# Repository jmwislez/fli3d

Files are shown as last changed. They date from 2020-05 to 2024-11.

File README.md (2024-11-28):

# The Fli3d Project

## Purpose

Fli3d (pronounced "flight") is a project by Jean-Marc Wislez for the 2020 (well, 2022) edition of the Belgian "Fri3d Camp" hacker event (https://www.fri3d.be/). Its purpose is to develop and launch an ESP32 payload on top of a microrocket.  And this payload needs to be as cool as possible ...

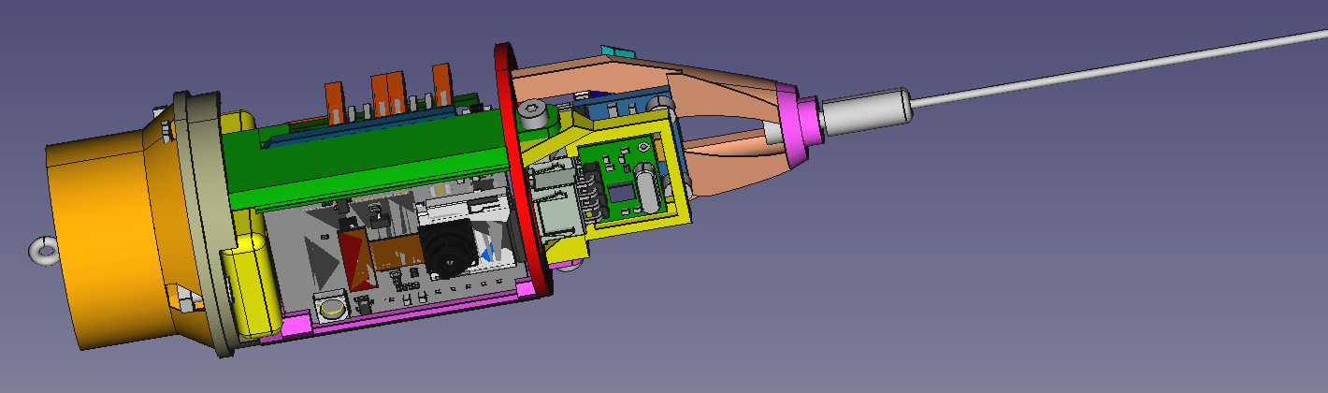
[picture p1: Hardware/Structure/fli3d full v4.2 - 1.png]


The name is obviously derived from "Fri3d Camp", and from the fact it's "flight hardware".

I have been working in the space industry for more than 20 years now, and this included design, building, testing and operations of payloads on Shuttle missions and ISS.  Basically I used this experience and the typical approaches here, but doing everything myself instead of collaborating in large teams.

## Overview

The Fli3d payload has roughly the size of a toilet paper roll, and weighs less than 100g.  Hardware costs for one v1 unit are below 25 euros.  The payload is intended for launch on a microrocket with minimally a B-motor.  The payload contains the following:
  - a 3D-printed structure and fairing
  - an ESP32 minikit MH-ET microprocessor board, running custom software (developed in Arduino IDE) to control all Fli3d subsystems and transmit live telemetry and receive commands over WiFi
  - an MPU6050 accelerometer/gyroscope sensor unit for determining accelerations and orientation
  - a BMP280 barometric sensor for determination of the rocket altitude
  - a NEO6MV2 GPS module, for determination of position and speed
  - an ESP32CAM module with an OV2640 camera and SD-card module, for image acquisition, in-flight image and telemetry storage, and live transmission of telemetry and images over WiFi
  - a WL102-341 433 MHz radio transmitter module, for in-flight transmission of selected telemetry
  - a 240 mAh Li-ION battery for standalone autonomy of 20 (TBC) minutes, with 134N3P charger for tethered operation or pre-launch charging
  - separation detection, for detection of opening of parachute compartment
  
All flight data is to be monitored live on a ground computer running Yamcs (open source software developed for ISS payload and satellite operations), and to be retrievable after flight, both physically and through file transfer.

A v2 version is under development with significantly improved functionality and also easier to assemble and test.  More information will be available soon ...

## Flights

To date, the payload has not flown yet.  It is hoped to do one or more test flights before Fri3d Camp in August 2020, and one or more demo flights at Fri3d Camp.

Each flight will be designated through a successive starting letter, and have a corresponding name:
  - Fli3d Aubergine [flew 18-Aug-2024 on a C-motor microrocket](https://github.com/jmwislez/fli3d/blob/master/Fli3d%20Aubergine%20-%20flight%20report.md)
  - Fli3d Banana 
  - Fli3d Chicken ([flew 25-Sep-2022 on a weather balloon](https://github.com/jmwislez/fli3d/blob/master/Fli3d%20Chicken%20-%20flight%20report.md))
  - Fli3d Dumplings
  - Fli3d Eggs
  - Fli3d Fries
  - ...
  - Fli3d Rice

Fli3d Chicken is not on a micro-rocket, but on a weather balloon.  [A special casing](https://github.com/jmwislez/fli3d/blob/master/HARDWARE.md#structure-for-weather-balloon-version) was developed for this configuration.

## Available documentation and repositories

  - https://github.com/jmwislez/fli3d :
    - Project introduction
    - Hardware design files
    - Yamcs (ground segment software) configuration
  - https://github.com/jmwislez/fli3d_esp32 :
    - Arduino IDE code for fli3d ESP32 MH-ET LIVE MiniKit
  - https://github.com/jmwislez/fli3d_esp32cam :
    - Arduino IDE code for fli3d ESP32-CAM
  - https://github.com/jmwislez/fli3d_lib :
    - Common Arduino IDE code for fli3d ESP32 MH-ET LIVE MiniKit and ESP32-CAM

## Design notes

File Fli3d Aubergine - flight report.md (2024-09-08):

# Fli3d Aubergine – flight report
## Main flight characteristics
Fli3d Aubergine was the first flight of the Fli3d payload on a microrocket.  It was the second flight of the Fli3d electronics. [Click here](https://github.com/jmwislez/fli3d/blob/master/README.md#flights) for an overview of the flights and their naming.

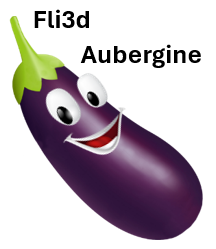
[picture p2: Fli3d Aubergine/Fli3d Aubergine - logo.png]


| Characteristic | Value |
| - | - |
| Launch date / time | 18-Aug-2024 12:41 CEST |
| Launch location | De Kluis, Sint-Joris-Weert, Belgium |
| Height (without antenna) | 50 cm |
| Height (with antenna) | 65 cm |
| Diameter | 35 mm |
| Mass | 145 g |
| Motor | C6-3 |
| Parachute | 45 cm by Klima |
| Fin: | 3D printed (3) |
| Stability number | 4.94 calibre |

[[Fli3d Aubergine photo album](https://photos.app.goo.gl/HriTFwFs2qNNNqe7A)]

## Ground segment
The ground segment set-up consisted of a Windows 10 laptop running [Yamcs 5.9.8](https://yamcs.org), a NodeMCU ESP8266 microcontroller running [fli3d-rx433](https://github.com/jmwislez/fli3d_rx433) for translating the telemetry packets received over radio (433.700 MHz) to UDP packets towards Yamcs, and a WRT-54GL router for creating a private 2.4 GHz Wi-Fi network with fixed IP address assignments for the rocket, laptop and radio receiver.

## System status before launch
The original Fli3d Payload [as described here](https://github.com/jmwislez/fli3d/blob/master/HARDWARE.md#fli3d-hardware) was flown.

The rocket software was way more stable than during Fri3d Camp 2022.  This is mainly thanks to some bug fixing, code clean-up to eliminate all compilation warnings for the Fli3d native code, and porting to the latest ESP32 core (v3.0.4) and libraries.  The software version was as below (tagged "aubergine" in repositories):

| Subsystem | Software version |
| - | - |
| ESP32 | [fli3d_esp32](https://github.com/jmwislez/fli3d_esp32/) v1.2.0 dated 2-Aug-2024 <br /> [fli3d_lib](https://github.com/jmwislez/fli3d_lib/) v1.2.2 dated 13-Aug-2024 |
| ESP32CAM | [fli3d_esp32cam](https://github.com/jmwislez/fli3d_esp32cam/) v2.2.0 dated 2-Aug-2024 <br /> [fli3d_lib](https://github.com/jmwislez/fli3d_lib/) v1.2.2 dated 13-Aug-2024 |

The only subsystem not working was the NEO6mv2 GPS receiver, that would not lock for unknown reasons.  This is an intermittent problem which I did not yet try to debug.  It is possibly linked to the positioning of the GPS antenna too close to other electronics (though it used to mostly work in the past).

The final assembly of the payload and rocket were achieved only just before flight. I had no time to do any further testing or preparations.  

Near the launch site I started all systems, checked system health and communication with the system.  All were as expected, though I found later that no packets were being received over 443.700 MHz radio. I sent the command to start the picture acquisition and brought the rocket to the launch ramp some 15 meters from there.

## Launch and Flight
The rocket was launched in between a series of smaller children’s rockets, in the idea to attempt a reflight with a stronger motor towards the end of the launch campaign.  I gave a short explanation, unplugged the tethering, installed the rocket on the launch platform and ignited the wick. 

The rocket left the launch pad properly and had a stable flight, which was a great relieve given its mass and top-loading.  It soon started flying much more horizontally than the smaller microrockets that day and had its culmination and separation above the surrounding woods instead of above the grass terrain. Separation was clearly visible, but the parachute could not be observed to deploy before visual contact was lost behind the trees.

The reason for the horizontal flight is twofold.  With the weight of the rocket, the launch pad rod bent, which accounted for a larger launch pitch than the smaller rockets.  The main factor is however that I designed the rocket to be significantly “overstable”, in fear of instability when leaving the launch rod.  With this feature, the rocket has a strong tendency to orient itself towards the wind, which is horizontal. 

## Recovery
Despite searching attempts, the rocket could not be found back after the flight.  The search area was too large, with large trees and brambles, with no visual hint on where to concentrate the search.

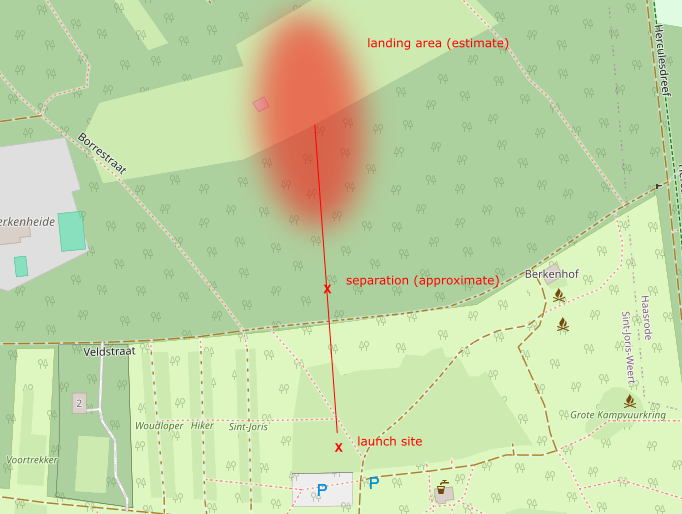
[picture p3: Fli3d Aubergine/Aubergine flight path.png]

<em>Approximate flight path and landing area</em>

After Fri3d Camp I made a poster which was hung there by staff from De Kluis and by Wouter Wuyts.  A few days later, I got a message from Sebastiaan Vileijn who had found the parachute hanging high in the trees at following coordinates: 50.801579 north,4.663138 east.  A few days later, he went back with binoculars and confirmed the rocket tube is hanging there too.  At the foot of the tree he found the fins.  It is not yet confirmed that the rocket nose is also in the tree, but I consider that probable.  I will be going there myself soon, and attempt a recovery with David Steeman.

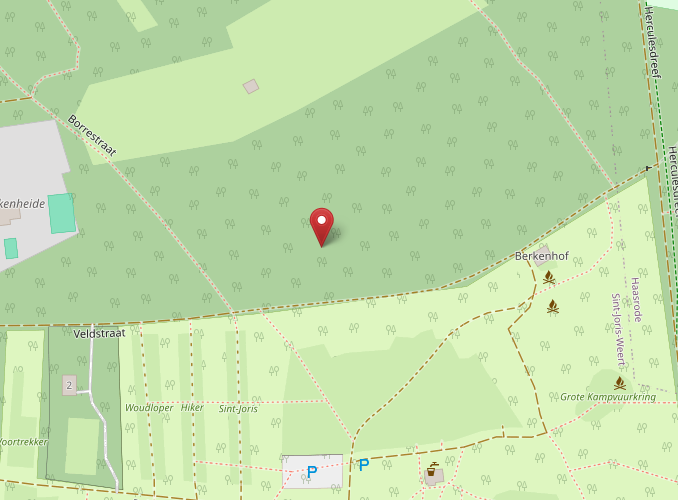
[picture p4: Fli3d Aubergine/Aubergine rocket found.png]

<em>Location at which rocket is hanging in a tree</em>

## Telemetry analysis

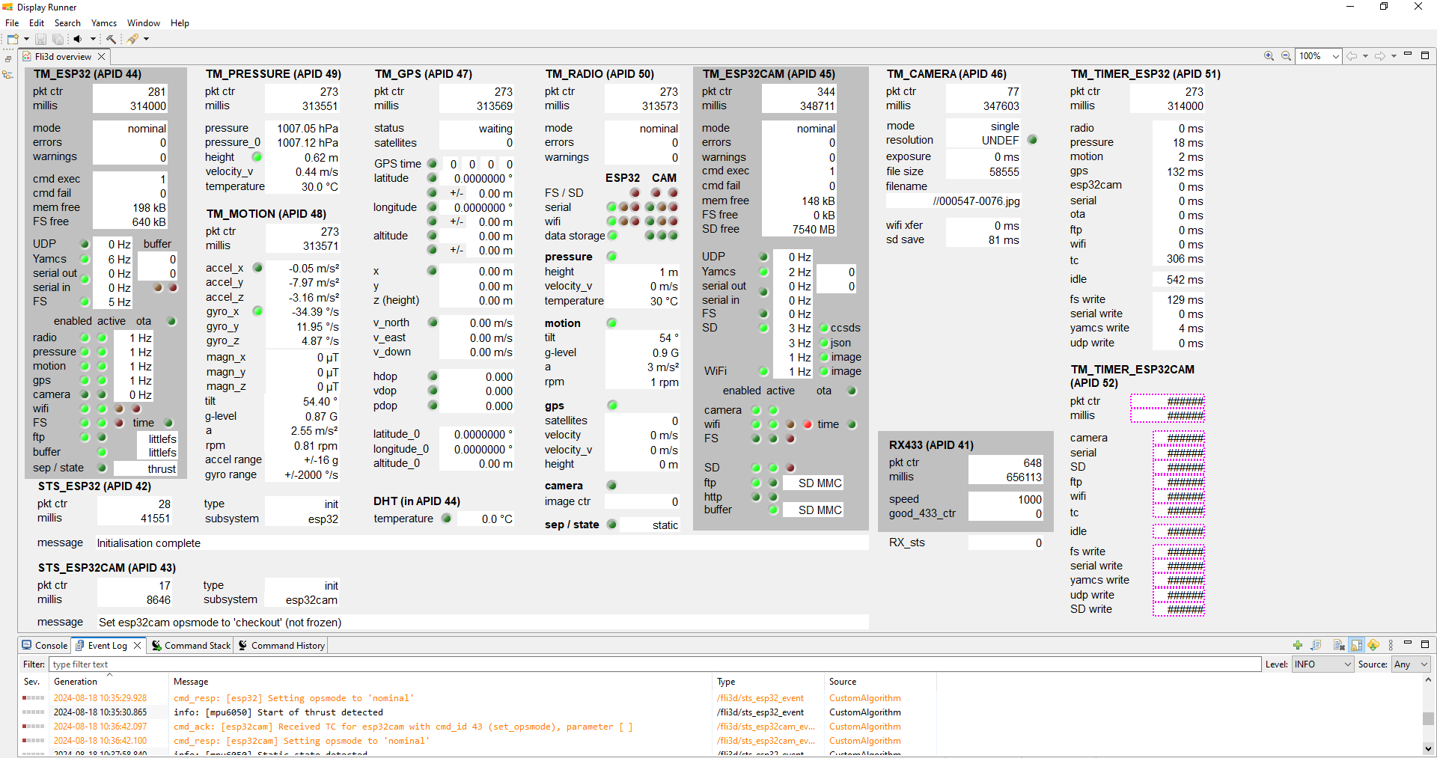
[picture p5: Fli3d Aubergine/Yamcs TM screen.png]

<em>Yamcs telemetry screen before flight</em>

Yamcs performed very well, and properly recorded all telemetry received.  From this, the following can be observed:
*	The rocket systems are booted at 10:32:17 UTC. All systems are nominal during the preparation phase, with the exception of known anomalies.
*	The camera starts acquiring at 10:36:42 UTC.
*	When taking the rocket to the launch pad, the quality of the Wi-Fi connection decreases, and packets are lost.  The 2.4 GHz Wi-Fi bands at Fri3d Camp are significantly overloaded and they perturbed my private network.  The 433 MHz transmission does not seem to have worked, which I failed to notice during check-out.
*	The moving of the rocket is visible from accelerometer data when I do the explanation.  
*	At 10:40:16 UTC, I untethered the rocket from the battery pack.  Both ESP32 in the rocket reboot due to this, very likely following a brownout detection (temporary low voltage).  I had seen this behaviour occasionally 2 years ago but forgot about it.
*	With the Fli3d Wi-Fi basestation drowning in the Fri3d Camp radio smog, the rocket did not connect back to the network and no further packets are received over Wi-Fi.  
*	With the reboot, the ESP32CAM camera is out of nominal mode, and thus stops taking pictures.  The camera was thus (again!) not working during the flight.  
*	With the reboot, the ESP32 altitude meter based on atmospheric pressure is in calibration status, and thus does not translate pressure changes in altitudes.
*	Three loose telemetry packets are then received over the 433.700 MHz radio channel, showing a proper reboot of all systems, but without Wi-Fi connection.
*	According to the datestamp of a picture taken by Jan De Bleser, the launch is at 12:41 local time, 10:41 UTC.
*	To my surprise, the telemetry archive contains a last packet received at 10:44:28 UTC, by when the rocket has landed already.  The telemetry does not contain much useful data, but it shows a static rocket with separation activated!  So the rocket still worked after landing, and 433.700 MHz radio did work over a longer distance (likely 100-200m).  The radio environment was just too noisy to receive more packets.
With the rocket unrecovered and Wi-Fi contact lost, the onboard telemetry could not be retrieved.  If the rocket is found by accident and returns to me by miracle, it may still be recoverable.

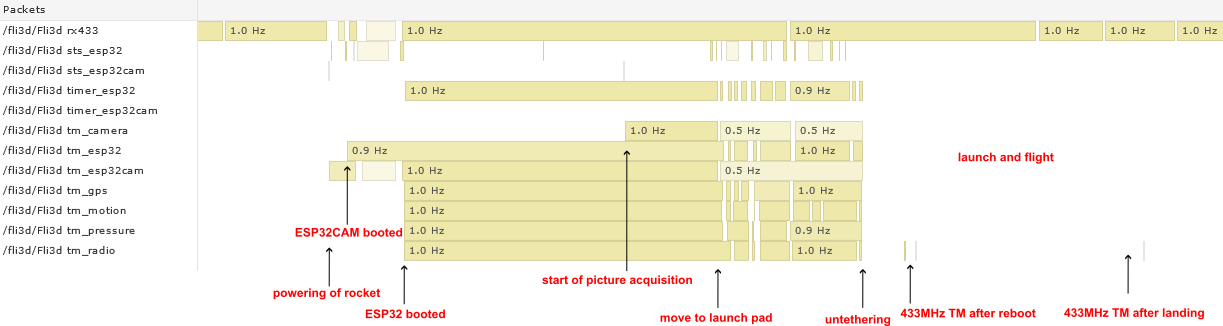
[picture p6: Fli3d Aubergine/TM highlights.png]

<em>Yamcs telemetry archive, with main events</em>

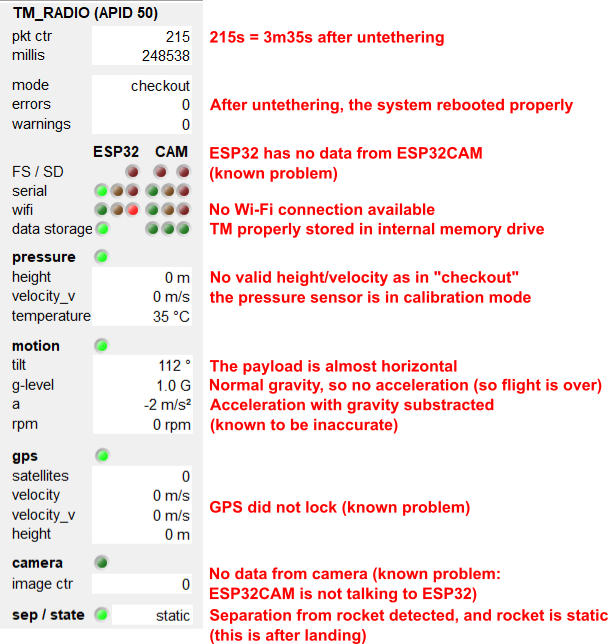
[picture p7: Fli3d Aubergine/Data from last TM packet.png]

<em>The last packet received, from after landing</em>

## Lessons Learnt
I compiled a detailed list of lessons learnt to guide the design of Fli3d Payload v2 towards future flights, but these are the main ones:
* The main lesson I learnt is that for achieving overall results, all aspects of the mission deserve attention.  I launched a pretty functional payload, but with too many uncertainties or improvisation on many other aspects.
* I should redesign the rocket length and fins to resolve the overstability.
* The only way to have reliable radio communication at Fri3d Camp is to migrate to 5 GHz wifi or to use a much stronger radio transmitter.
* I should better know the speed at which the memory of the rocket fills and the battery depletes.  Now I felt in a hurry to launch, while that was likely not necessary.
* I should implement means that facilitate recovery of the rocket after landing: bright colours, buzzing sound, flashing light, contact information on rocket, portable radio receiver, airtag, etc.

## Acknowledgements
Thanks to the organizers of Fri3d Camp for creating the inspiring environment that made me build this rocket payload and created a forum for sharing this project with others.

Thanks to Benny Geys for providing the launch facilities and practical support regarding the rocket.  Thanks also to David Steeman for searching the rocket, even if unsuccessful!  

Finally, I am grateful to Mieke Praet for gracefully granting me the time and space to play.

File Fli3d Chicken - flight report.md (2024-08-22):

# Fli3d Chicken - flight report

## Main flight characteristics

Fli3d Chicken was the maiden flight of the Fli3d electronics.  It was a weather balloon flight.

The flight was hit by many problems. Network problems at the launch site prevented check-out and configuration of Fli3d Chicken, and due to this the camera was not activated during flight.  During the flight, the electronics and software performed moderately well.  When the balloon 
reached 37km and burst (expected behaviour), Fli3d Chicken got ripped off its hook, and came down in freefall.  It survived the crash very well: all electronics is still working.  

Despite the problems, a load of interesting engineering data and experience were gathered, that will significantly contribute to improving the Fli3d system.  This page collects and presents all this experience. 

| Event | Details |
| - |- |
| Platform | IRM/KMI weather balloon<br />ON4IR-3 tracker |
| Launch | 25/09/2022 15:18:31 UTC<br />IRM/KMI Uccle, Belgium |
| Burst | 25/09/2022 17:26:35 UTC<br />at 37085 m altitude<br />Rupture from parachute line and start of freefall, with speeds up to 700 km/h |
| Crash | 25/09/2022 17:39:58 UTC<br />in a field near Eppe-Sauvage, France (76.86 km distance), at 65 km/h |
| Duration | Ascent: 2h08m03s<br />Descent: 13m25s<br />Total: 2h21m28s |

[[Fli3d Chicken photo album](https://photos.app.goo.gl/S38xrLcGTVrPPzQt9)]

## Pre-flight preparations

### Set-up and operational approach

The set-up consisted of a laptop, connected to internet through a smartphone access point, and providing a "Fli3d" private network access point for pre-flight communication with Fli3d Chicken using the MyPublicWifi software.

A [checklist for launch preparations](https://github.com/jmwislez/fli3d/blob/master/Fli3d%20Chicken/Fli3d%20Chicken%20procedure.xlsx) was prepared (dry-run at home before).

### Known issues

The Fli3d software/system is still under development, and by the time of the launch, the following issues were known (and all hit):

- intermittently, GPS module would not lock
- Real-Time-Clock module (last minute addition) on ESP32CAM not tested
- Spontaneous reboots happen occasionally
- Occasional frying of SD cards
- FTP to ESP32CAM flash filesystem unstable

### Pre-flight anomalies

One of the very first steps, starting the Yamcs server for Telecommand/Telemetry communication with Fli3d, failed.  Afterwards, this turned out to be the consequence of a hidden and unnecessary network dependency from my home network.  It has been recognized as an issue to be fixed in Yamcs, and a work-around would have been activating my VPN connection to home.  But I did not thinks of that ...

Without Yamcs, any verification of Fli3d Chicken and any configuration commanding was impossible.  I could only confirm through MyPublicWifi that both ESP32 were connected to the WiFi, hence active.

Mandatory commanding was to set both ESP32 from "checkout" to "nominal" operations mode, and to freeze them in that mode in case of spontaneous reboots.  For ESP32 this just sets some internal processing of acquired data, but for the ESP32CAM, this starts the camera frame grabbing.  Crucial ...

The effect of the freezing command is to create an "opsmode.lock" file on the filesystem, with one 0x02 character, indicating a reboot in mode 2 (nominal).  So I created such file (with help of my radioamateur friends), and put it on ESP32 (flash file system over FTP) and ESP32CAM (physically on SD card).

The ESP32CAM SD card just fried at that moment, so I had to take a new one.  After the faulty SD card, I also had to reboot my computer for the new SD to work.  At the last moment, I also added the latest configuration files on the SD card.  The latter I should not have done ...  These configuration files tell ESP32CAM to look for the "opsmode.lock" on the flash file system, while the default is the SD card.  Hence, during flight it did not find the file, and ESP32CAM stayed in "checkout" mode, without taking pictures ...

Also, with rebooting the laptop and not the MyPublicWifi software, the ESP32s could not acquire an NTP time reference before launch.

### Handover and launch

Due to the anomalies closure of the Fli3d Chicken box was done very fast and without checks, since there was a crowd waiting for the now delayed launch.  The ON4IR-3 tracker was taped to Fli3d Chicken with duct tape, and the rope of the balloon was knot to the hook on Fli3d Chicken.  No time for configuration pictures.

I got the occasion to explain Fli3d Chicken to the audience, in French and in Dutch, and let Fli3d rise in the blue-patched sky ... [[Facebook video](https://www.facebook.com/gaetan.horlin/videos/755262105775191)]

## Flight

The ON4IR-3 tracker, provided by the radio amateur community, worked flawlessly throughout the whole flight, and allowed for easy remote tracking and real-time landing site prediction.  

The timestamping of the events below is performed by correlation of ON4IR-3 GPS timestamp and events with ESP32 relative timestamps and measurements.  A deviation of up to 10 seconds is possible.

| Time in flight | Timestamp (UTC) | Altitude | Event / comments |
| --- | --- | --- | --- |
| -0:06:25 | 25/09/2022 15:12:06 | 100 m | Power-up of Fli3d Chicken for flight |
| 0:00:00 | 25/09/2022 15:18:31 | 100 m | Balloon release |
| 0:06:50<br />0:20:11<br />0:32:59<br />0:45:47 | 25/09/2022 15:25:20<br />25/09/2022 15:38:42<br />25/09/2022 15:51:29<br />25/09/2022 16:04:17 | 2050 m<br />5704 m<br />8895 m<br />12261 m | ESP32 reboots |
| 0:55:08 | 25/09/2022 16:13:38 | 14708 m | BMP280 sensor stops |
| 0:59:24<br />1:16:24<br />1:33:15<br />1:49:24 | 25/09/2022 16:18:16<br />25/09/2022 16:35:21<br />25/09/2022 16:52:16<br />25/09/2022 17:08:30 | 16012 m<br />20922 m<br />26205 m<br />31600 m | ESP32 reboots |
| 2:08:03 | 25/09/2022 17:26:35 | 37085 m | Balloon burst, rip-off of hook, and ESP32 reboot |
| 2:21:28 | 25/09/2022 17:39:58 | 186 m | Crash landing of Fli3d Chicken and ON4IR-3 at 65 km/h, after freefall |
| 2:26:27 | 25/09/2022 17:44:57 | 186 m | ESP32 reboot |
| 2:43:53 | 25/09/2022 18:02:23 | 186 m | Pick-up by recovery team |
| 2:45.38 | 25/09/2022 18:04:09 | 186 m | ESP32 reboot |
| 2:55:41 | 25/09/2022 18:14:12 | 186 m | Deactivation by recovery team |

## Post-landing videos

Fli3d Chicken/VID-20220925-WA0020.mp4

![Fli3d Chicken/VID-20220925-WA0021.mp4]([https://github.com/jmwislez/fli3d/blob/master/Fli3d%20Chicken/VID-20220925-WA0021.mp4](https://raw.githubusercontent.com/jmwislez/fli3d/master/Fli3d%20Chicken/VID-20220925-WA0021.mp4))

## System performance assessment

| **Subsystem** | **Lessons** | **Suggestion for next version** |
| --- | --- | --- |
| **Network** | Ok! <br />Worked out of the box and connection with 2 ESP32s was visible shortly after start-up. | MyPublicWifi is ideal for pre-launch configuration and check-out, and for quick set-up in a foreign environment.  For in-flight data acquisition, the range of a MyPublicWifi is likely too limited and real network infrastructure is preferred. |
| **Yamcs** | Hung during startup, waiting for (unneeded) home network.  Confirmed bug in Yamcs.<br />This problem prevented check-out and configuration of Fli3d Chicken before flight. | Update yamcs server after bug fix. <br />Try connecting to Home VPN if re-occurrence.<br />Yamcs has always been very stable though, so this was just Murphy. |
| **Housing** | Excellent thermal isolation: minimal internal temperature was -21.5 degC, while external temperature at -40 degC or maybe worse.  <br />Excellent shock protection:  electronics operations continued uninterrupted at 65 km/h impact, after 37km freefall.  All electronics survived crash.<br />Attachment hook got loose at burst (aluminium tape ruptured). | Make inner volume slightly larger for easier harness accommodation.<br />Anchor the hook to the structure, and not only to the easily shearable aluminium tape layer.  <br />Potentially add an elastic, to reduce shock on hook at burst. |
| **Battery** | Ok!  <br />Type: POWERFULL 708960 Li-Ion Batery Power Bank - 5000 mAh (bought at Colruyt)<br />Survived temperatures down to -21.5 degC.  Provided power throughout the full flight, and still full at 3/4 after recovery. | Spare power is available for additional electronics or heaters.  <br />Smaller/lighter battery can be considered. |
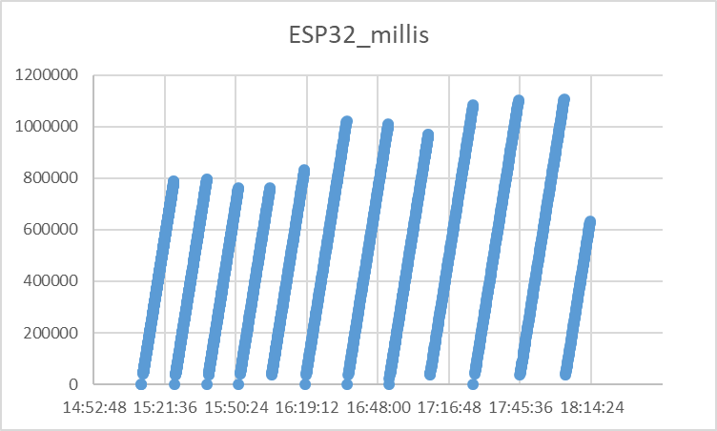
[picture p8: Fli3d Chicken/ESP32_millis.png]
Fli3d Chicken/ESP32_millis.png
| **ESP32** | Worked throughout the whole flight.<br />Rebooted 12 times over flight, at relatively regular interval, so likely software-induced rather than hardware/thermal problems.<br /> | Debug software for reboot cause.<br />Improve resilience/continuity in case of reboot. |
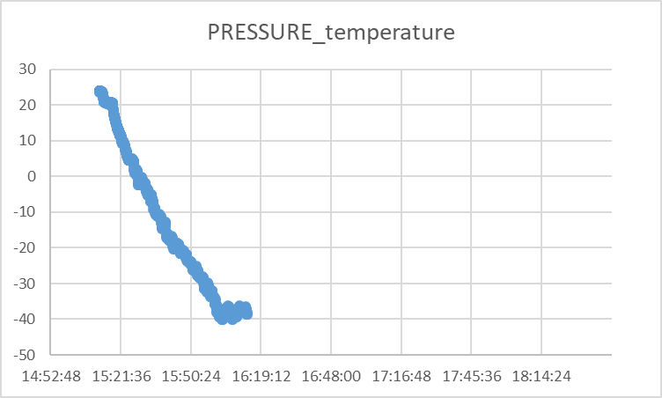
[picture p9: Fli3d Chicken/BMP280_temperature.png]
Fli3d Chicken/BMP280_temperature.png
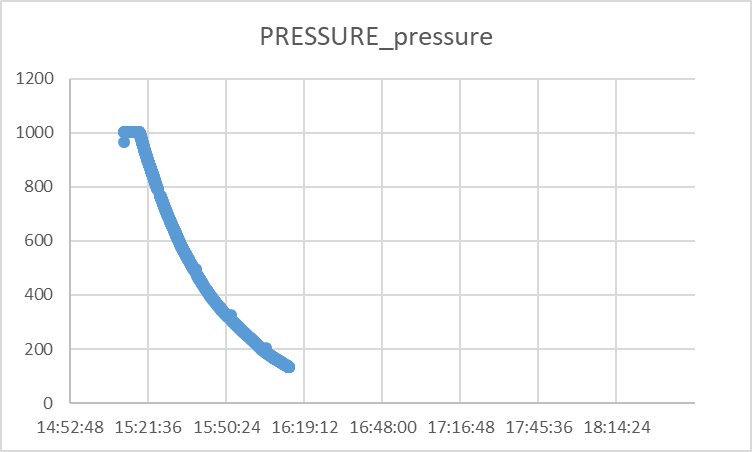
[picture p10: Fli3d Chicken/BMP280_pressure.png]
Fli3d Chicken/BMP280_pressure.png
| **BMP280** | Good temperature and pressure measurements down to -40 degC / 134 mbar.  At the end of the measurements, temperatures were stable, fluctuating between -36.5..-40 degC. <br /><br /><br />Worked properly after a post-landing reboot. | Datasheet range of BMP280 is 300..1100 hPa, -40..+85 degC, so malfunction at the observed pressure/temperature is not unexpected.<br />Suggest to put BMP280 inside the housing for pressure measurements, and use an external passive temperature sensor (PT100 or similar). |
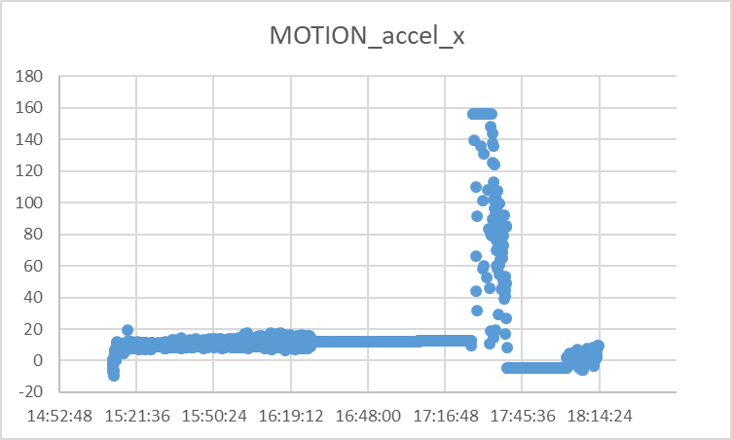
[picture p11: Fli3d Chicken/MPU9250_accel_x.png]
Fli3d Chicken/MPU9250_accel_x.png
| **MPU9250** | Worked properly throughout the full flight.<br />Acceleration sensor data clearly show the different phases, but further interpretation is difficult.  During the freefall, the accelerometer gets saturated occasionally, while its range was set to +/- 16G.  The ride down was bumpy ...  <br /><br />Gyroscope date show mainly rotations around the X-axis (vertical axis of Fli3d Chicken) during ascent, and random during descent.  Rotations of 100-200 deg/s are common, so many pictures would have been blurry. At the highest altitudes, the probe clearly stabilises.  Y and Z axes are more stable.  The head-down orientation of the crashed Fli3d Chicken is visible in the data.<br />Fli3d Chicken/MPU9250_gyro_x.png<br />Instantaneous absolute orientation of Fli3d Chicken could be derived from the magnetometer, but without camera this information is of limited value. | Think of stabilisation means for imaging: mechanical/electronic stabilizers, or simply fins.<br />Check whether one more significant number is possible in the magnetometer telemetry. |
| **GPS** | The GPS never locked on a signal during flight.  From the recovery video, it is visible that there is no GPS light red flashing, so the lack of lock is at hardware level.  Intermittent unability to lock has been regularly observed during development and is not yet understood.  <br />The very same GPS board has been observed to work since (in open box configuration).<br />Without GPS data, ESP32 had no absolute time reference during flight. Hence, all events needed to be correlated post-flight. | Assess why GPS  sometimes does not lock.  Assess whether the aluminiumless window for the antenna is sufficiently large, whether there is a preferred antenna orientation, if the antenna connector always properly connects.<br />Consider external antenna. |
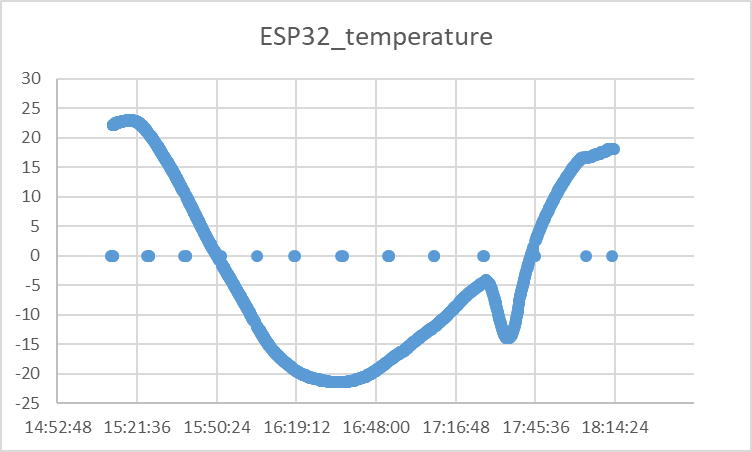
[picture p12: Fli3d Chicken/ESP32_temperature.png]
Fli3d Chicken/ESP32_temperature.png
| **DHT22** | Worked flawlessly during the flight, and proved good performance of the thermal isolation.  The temperature initially decreases during freefall, which is likely due to the breaching of the thermal isolation with the rip-off of the hook.<br /> | Indeed interesting to include an internal temperature sensor (last minute addition) |
| **ESP32CAM** | **TBW** | |
| **Camera** | No pictures due to hack not working …<br />Camera worked properly post-flight. | |
| **SD card** | Worked well during flight (for ESP32CAM TM storage, no images)<br />Fried one SD just before flight. | Assess why so often an SD card is fried |
| **RTC** | **TBW** | |
| **In-flight TM archive** | CCSDS TM archive present (recovered from ESP32 FS through FTP and ESP32CAM SD physically) and error-free, but no time information available.<br />Not all status messages seem to have been recorded. | Include replay functionality in software<br />Introduce secondary header with absolute timestamps<br />Assess completeness of archive. |
| **Operational** | Time-pressured after anomalies, let go for flight without confidence in readiness. | Dry-run on field.  <br />Develop "what-if" for the full preparation procedure.  <br />Do initial check-out  hours before, even if done at home, and foresee full development and checkout  environment on-site. |
| **Software** | The ESP32/ESP32CAM software performed well throughout flight, with the following observations:<br />* ESP32 rebooted at almost regular intervals, hinting a software problem<br />* Commanding is mandatory  to start acquisition, and for checkout<br />* The hack worked for ESP32 (moved  to "nominal" opsmode after each reboot)<br />* The hack did not work for ESP32CAM (stayed in "checkout" opsmode after each reboot)<br />* There was no way to start the camera without commanding<br />* The use of SD or FS is fully configurable, which adds possibility for configuration errors, and prevented the hack to work.  In general, the software may be too configurable,  which can lead to errors<br />* FTP not working for accessing ESP32CAM SD/FS | Debug reboots (when permanently disconnected from WiFi?)<br />Think of simple possibilities to confirm proper operations and configure minimal flight configuration without TC/TM<br />Cleanup SD/FS, and  think of SD/FS data accessibility |
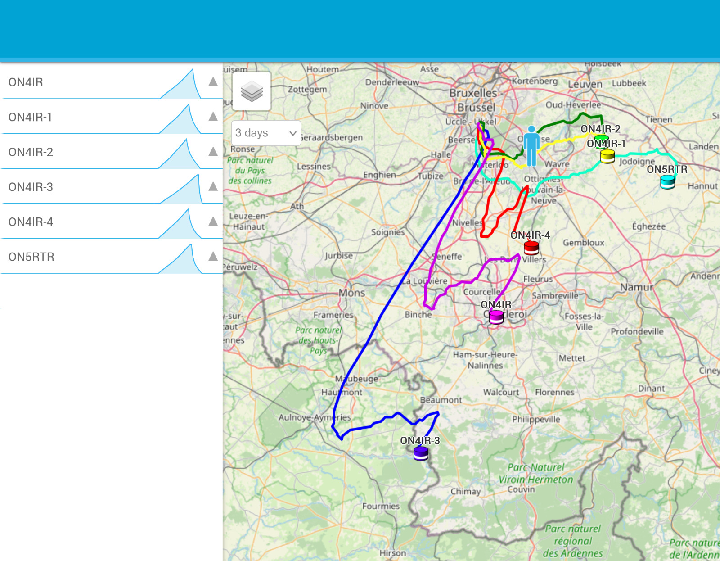
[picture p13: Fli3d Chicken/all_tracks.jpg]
Fli3d Chicken/all_tracks.jpg
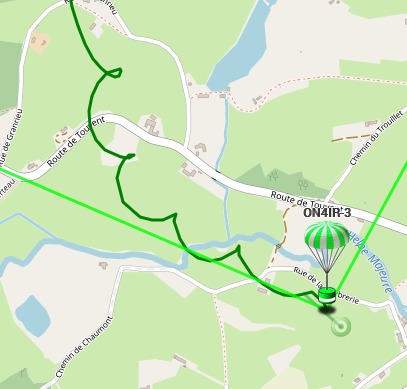
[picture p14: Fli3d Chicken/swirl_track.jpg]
Fli3d Chicken/swirl_track.jpg
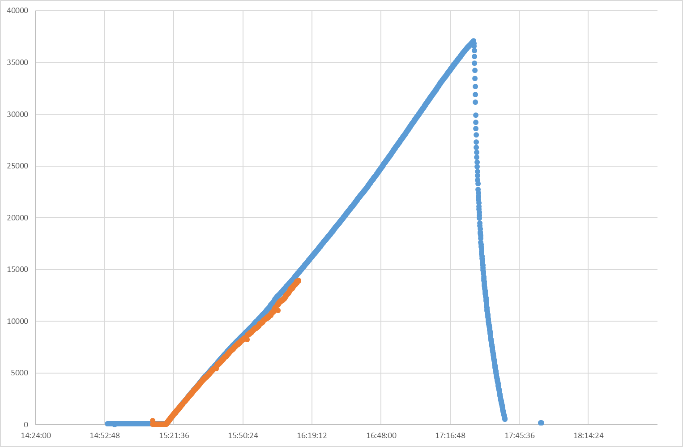
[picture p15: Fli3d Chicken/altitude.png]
Fli3d Chicken/altitude.png
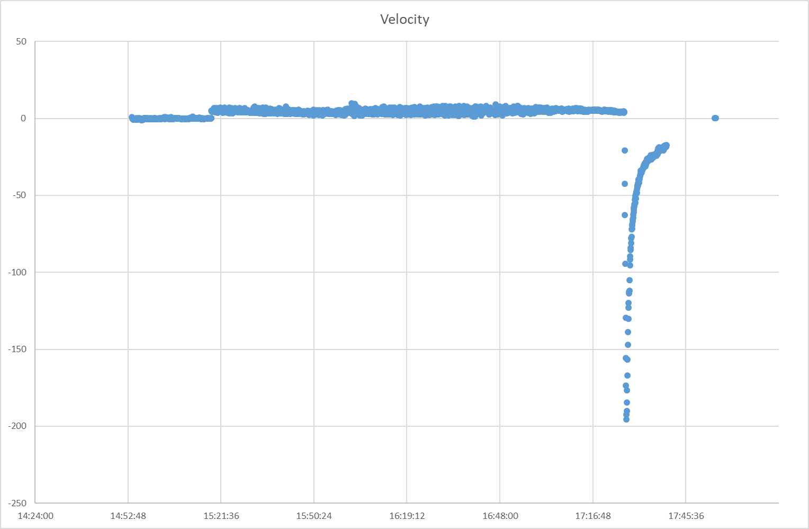
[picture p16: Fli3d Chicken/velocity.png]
Fli3d Chicken/velocity.png
| **ON4IR-3** | Not part of Fli3d Chicken.  Worked flawlessly, and was invaluable in post-processing the data.<br />ON4IR-3 acquired GPS positioning and altitude data, as well as horizontal and vertical velocity.<br />The flight track (blue) shows how the balloon flew to the north of France.  Burst was at the last sharp turn in the track.  Details of the track just before landing show the swirling trajectory of Fli3d Chicken.<br /><br /><br />The figure below shows the correlation between the GPS altitude (blue) and the pressure/temperature derived altitude (orange).<br /><br />The vertical velocity graph below shows a steady upward velocity of on average 4.77 m/s.  After burst, freefall goes initially up to 195 m/s (700 km/h)! After that, it is slowed down by air friction up to 18 m/s (65 km/h).  Signal is lost 20 seconds before the crash (no line-of-sight).  ONI4R-3 was still working after the crash.<br /> | This module saved the mission! |

## Acknowledgements

Many thanks to IRM/KMI for this unique and amazing flight opportunity!  

I'm also very grateful to the very kind radio amateur team, for providing the ON4IR-3 tracker (with batteries!), the support before launch, the tracking infrastructure, the field recovery and shipping of Fli3d Chicken, and the very careful documenting of each step with nice videos.  You guys are delightful!  Special thanks to Manoel, Benoit and Olivier.

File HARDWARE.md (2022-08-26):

# Fli3d Hardware

## Overview
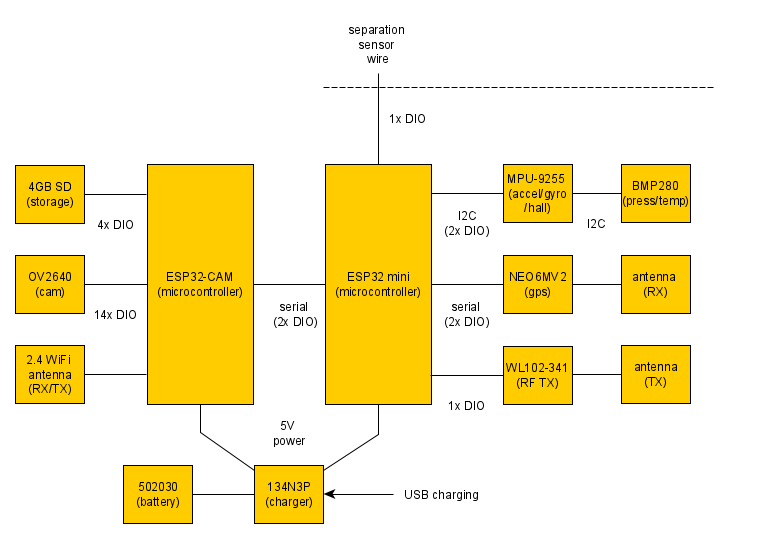
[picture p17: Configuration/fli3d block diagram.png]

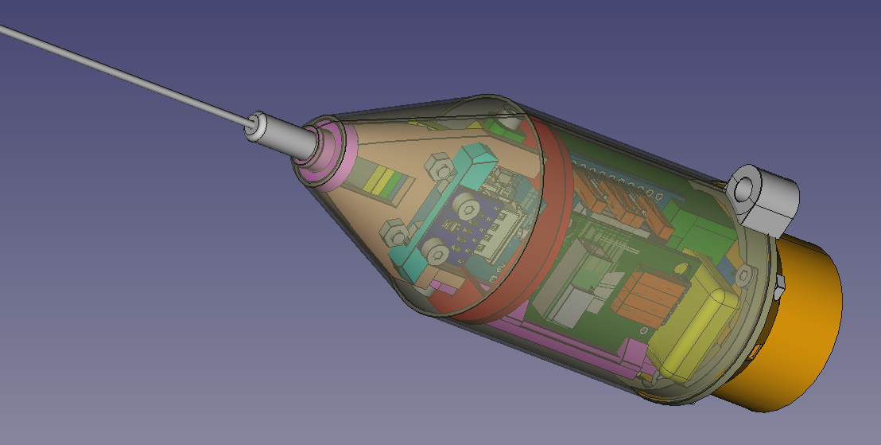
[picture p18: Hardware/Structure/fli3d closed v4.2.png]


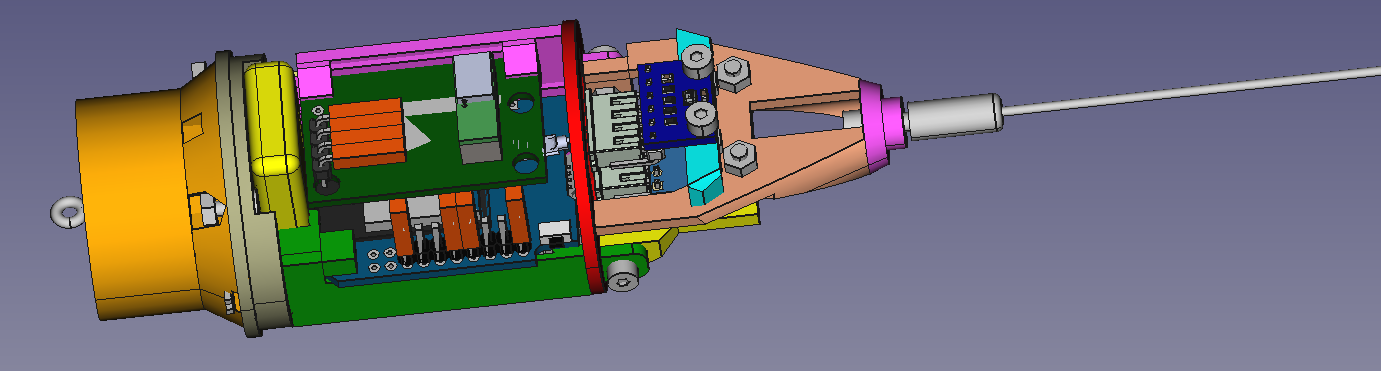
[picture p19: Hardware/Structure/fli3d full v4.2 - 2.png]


## ESP32 minikit MH-ET Live

Originally, I intended to use a Wemos D1 mini (ESP8266) microprocessor board as the core system for Fli3d, given its small size.  I however bumped into performance limitations when trying to acquire data from all sensors in parallel, and the ESP8266 has only one hardware serial port.  A second serial port had to be implemented in software, which added to the performance problems.

Also very small but much more powerful is the ESP32 minikit MH-ET Live board.  It looks very much like the D1 mini. A subset of its pins is even designed to be directly mapped to the D1 mini pinout.



This board is connected to the other Fli3d subsystems as follows:
  - powered at 5V by the 134N3P battery charger
  - serial connection to ESP32CAM on pins IO1 (TX) and IO3 (RX) at 115200 baud
  - serial connection to NEO6MV2 GPS receiver on pins IO17 (TX) and IO16 (RX) at 57600 baud
  - I2C bus to MPU6050 accelerometer/gyroscope and BMP280 pressure sensor on pins IO21 (SDA) and IO22 (SCL)
  - separation detection wire on pin IO19 (GND is mated, open is unmated)
  - WL102-341 radio transmitter with OOK signal on pin IO26
Note that not any combination of pins works, as there seem to be hidden conflicts between functionality.  In this configuration, all subsystems seem to be working well and independently.
  
The software was developed in Arduino IDE, and can be found in the following repository: https://github.com/jmwislez/fli3d-esp32 

I defined a basic 3D model of the board in FreeCAD: https://github.com/jmwislez/fli3d/blob/master/Hardware/Electronics/ESP32%20mini%20kit/ESP32minikit.FCStd

Some more details on this board's hardware: https://riot-os.org/api/group__boards__esp32__mh-et-live-minikit.html

The board costs less than 2 euros, and weighs only 8 g.

## AI Thinker ESP32-CAM

This neat little board includes a 2 megapixel (1600x1200) OV2640 colour camera with lens, an ESP32 microcontroller, and an SD-card adapter.  It merely weighs 8.5g, and costs less than 5 euros.



The camera is of course not very fast, and wifi transmission and storage further slow it down.  At low resolution, frame rates can be 25 Hz or higher.  At full resolution, this is rather 1 Hz.

The board interfaces to the ESP32 minikit over the serial connection.  All acquired telemetry is exchanged in both directions, so that both units have the full telemetry to send over WiFi, for redundancy.  Telemetry and images are stored on the SD card.  The SD card can also contain a configuration file, which allows to override default WiFi settings.

The ESP32-CAM module allows the connection of an external WiFi antenna.  For this, it is however needed to unsolder and resolder a tiny SMD bridge connection on the board.  I attached a laptop WiFi antenna, but did not yet do the rerouting.  I intend to test whether the external antenna does yield a better WiFi range.

Note that the ESP32-CAM module is slightly more cumbersome to flash than other development boards.  It does not feature an USB connector, so the flashing needs to be done via an USB to serial converter.  It is also needed to ground GPIO0 during flashing, and unground the pin and press the reset button in order to run the firmware.  So that's a lot of small manipulations, especially if the serial interface needs to be rewired after flashing.  Hence OTA update is strongly preferred, using "minimal SPIFFS" partitioning.

Most ESP32 connectivity is in use by the camera and SD card module, so do not expect to squeeze any more out of this module.  There is even a double use of pin GPIO 4, which makes the on-board flashlight blink when addressing the SD card.  This is annoying, but unavoidable by hardware design.  

The software was developed in Arduino IDE, and can be found in the following repository: https://github.com/jmwislez/fli3d-esp32cam 

A schematic of the board is available here: https://github.com/jmwislez/fli3d/blob/master/Hardware/Electronics/ESP32-CAM%20microcontroller%20%2B%20camera/ESP32_CAM_V1.6.pdf

## NEO6MV2 GPS sensor

It is astonishingly easy and cheap to integrate GPS functionality.  The NEO6MV2 board has all you need and can provide up to 16 readings per second, for slightly more than 6 grams (including antenna) and slightly more than 3 euros.

The GPS module is connected to ESP32 minikit over serial at 57600 baud.  Default speed is 9600 baud.  I tried 115200 baud too, but sometimes the serial line would not synchronize at that speed.

I defined a basic 3D model of the board in FreeCAD: https://github.com/jmwislez/fli3d/blob/master/Hardware/Electronics/NEO6MV2%20gps/neo6mv2.FCStd

The user manual is here: https://github.com/jmwislez/fli3d/blob/master/Hardware/NEO6MV2%20gps/U-blox-6-Receiver-Description-Including-Protocol-Specification.pdf

## MPU6050 accelerometer/gyroscope sensor

The MPU6050 provides a 6 DOF motion sensor over an I2C bus.  It provides passthrough functionality, which is used to connect the BMP280 sensor.  Initially I had hoped to use the sensor for internal navigation, i.e. determine position, speed, and orientation by integrating the acceleration/gyroscope readings.  The sensor is far from being sufficiently precise for this: it is even non trivial to get some usable data out of it.  There is a Digital Motion Processor on-board, but this functionality was hard to use, looked unstable to me, and did not help me to get what I needed.  Hence, I ended up doing my own naive calibration, which for now is still worthless.   

In a next version of Fli3d, it's probably worth looking at MPU9255, which also includes a 3D compass and can therefore more reliably provide orientation.  That board is slightly bigger, and would require a mechanical redesign of the Fli3d structure.

Mechanically, the board is mounted so that the sensor is on the rocket's central axis.  The X/Y/Z axes of the sensor correspond to Z/X/Y axes of the rocket.

The documentation of the board is extensive (https://github.com/jmwislez/fli3d/tree/master/Hardware/Electronics/MPU6050%206DOF%20motion%20sensor/), but lacks precision to harvest the full power of the chip.

## BMP280 barometer sensor

The BMP280 is a small, simple, but neat little board with a very sensitive barometer and thermometer, which can be used to determine altitude changes.  The resolution of altitude measurements is typically better than 1 meter!  

The board is connected over I2C, as an auxiliary board of the MPU6050.

The user manual of the chip is here: https://github.com/jmwislez/fli3d/blob/master/Hardware/Electronics/BMP280%20pressure%20sensor/BST-BMP280-DS001-11.pdf

## WL102-341 433MHz radio transmitter and antenna

Not knowing the stability of the WiFi connection in flight, I decided to add a 433 MHz transmitter on board, for transmission of a summary of the telemetry.  Moreover, this could serve as a beacon for Doppler measurements, which could later be correlated to the determined flight path.  This is not done yet.

This is the only board in the stack that needs to be powered at 3.3V instead of 5V.  This power is provided by the ESP32 minikit board.

The signal feeding the transmitter is digital output IO26 of the ESP32 minikit board, and this OOK (on/off keying) signal is then transmitted as is by switching the transmitter on and off.

The antenna for the 433 MHz is screwed on top of the rocket, and also holds the fairing in place.

## Battery and 134N3P battery charger

The on-board battery is a 300 mAh 3.7V Li-ION battery.  This provides an autonomy of roughly 20 minutes for a fully active system.  

The battery is not directly driving the Fli3d electronics, but connected to a 134N3P battery charger.  This is basically a circuit as used in power banks.  It converts the battery output to a steady 5V, it allow charging the battery, and while connected for charging, 5V is neatly provided.  Hence, it allows for tethered operations, and just before launch the power tether can be detached, and Fli3d is seamlessly on autonomous power with a fully charged battery.

Mechanically, the type A USB connector on the board needs to be unsoldered.  

## Wiring

There is not much physical space available for wire routing or connection.  Originally, I intended to use directly soldered wire connections for reliability, and to unsolder the headers where the boards came with headers pre-mounted.  The latter was not easy given my limited soldering skills and equipment, so I decided to keep the headers and use a combination of header sockets and direct soldering.

Friction connectors without latching do not perform well under mechanical stress, and the assembly is fragile and hard to repair.  Hence, the haressing is something that could definitely be improved.

Two rows of 8-pin female 2.54mm sockets are used for VCC and GND distribution.

An overview of the wiring connections is given below.

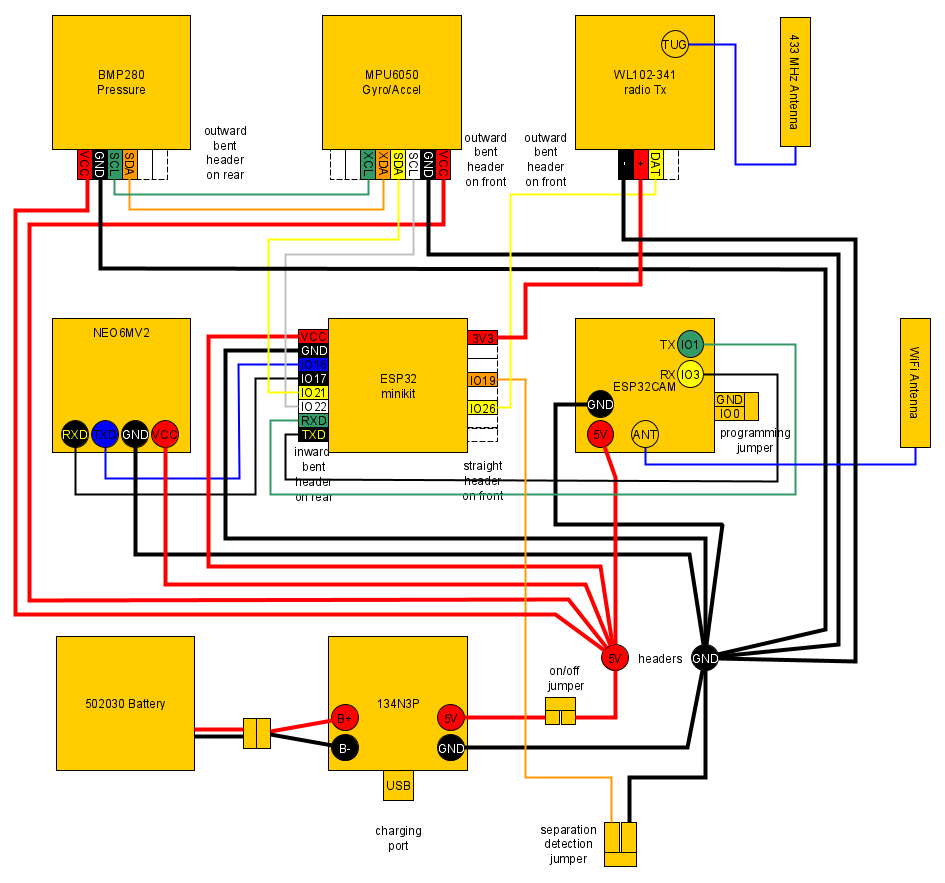
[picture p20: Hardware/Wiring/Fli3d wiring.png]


## Structure for micro-rocket version

The Fli3d structure was designed using FreeCAD, and is 3D printed with PLA on a Prusa i3 clone printer.  Total mass is 30 grams.  Assembly is mainly done with M2.5 screws and contact glue.

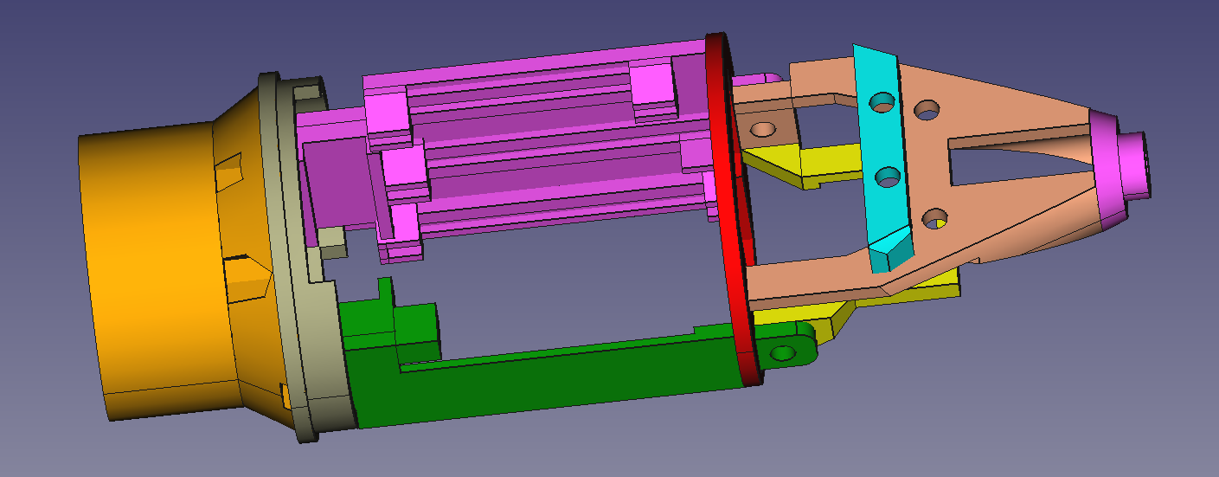
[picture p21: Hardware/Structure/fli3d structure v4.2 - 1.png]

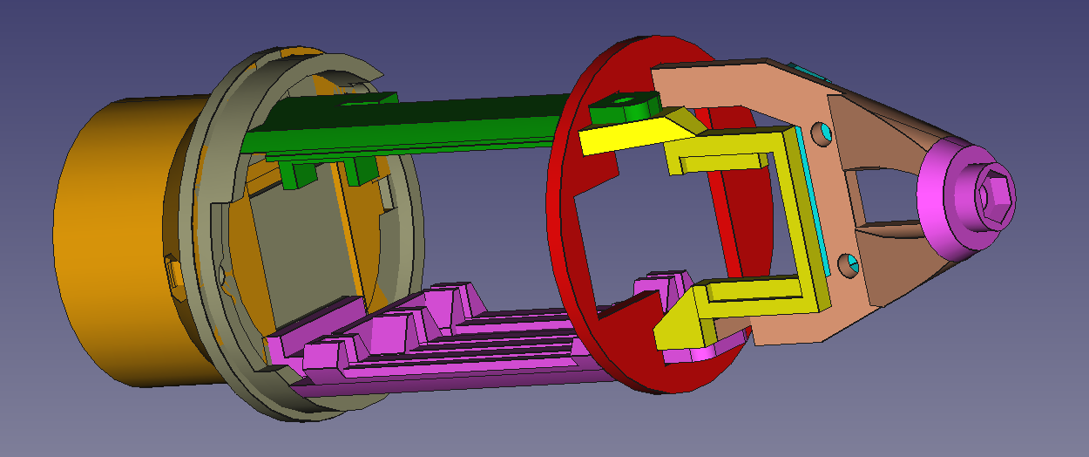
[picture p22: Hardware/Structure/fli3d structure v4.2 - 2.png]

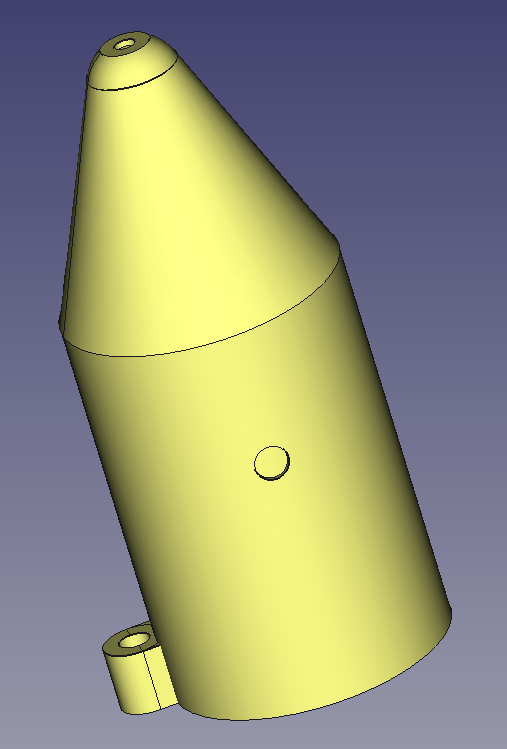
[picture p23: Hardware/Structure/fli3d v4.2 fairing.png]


The FreeCAD design files are here: https://github.com/jmwislez/fli3d/tree/master/Hardware/Structure

Each structural element coloured differently needs to be printed separately.

# Structure for weather balloon version

Another version of the structure was produced for flying Fli3d on a weather balloon, for flight "Fli3d Chicken".  

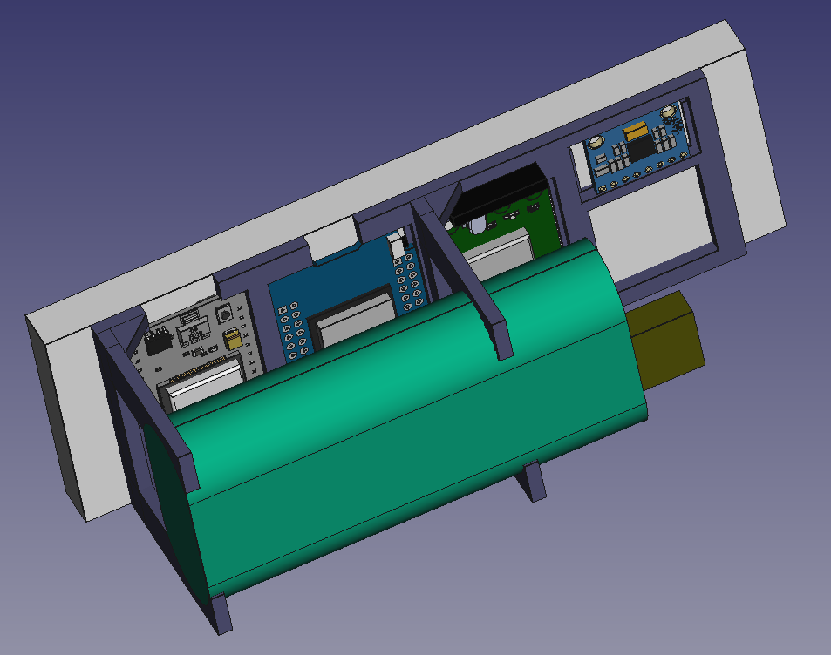
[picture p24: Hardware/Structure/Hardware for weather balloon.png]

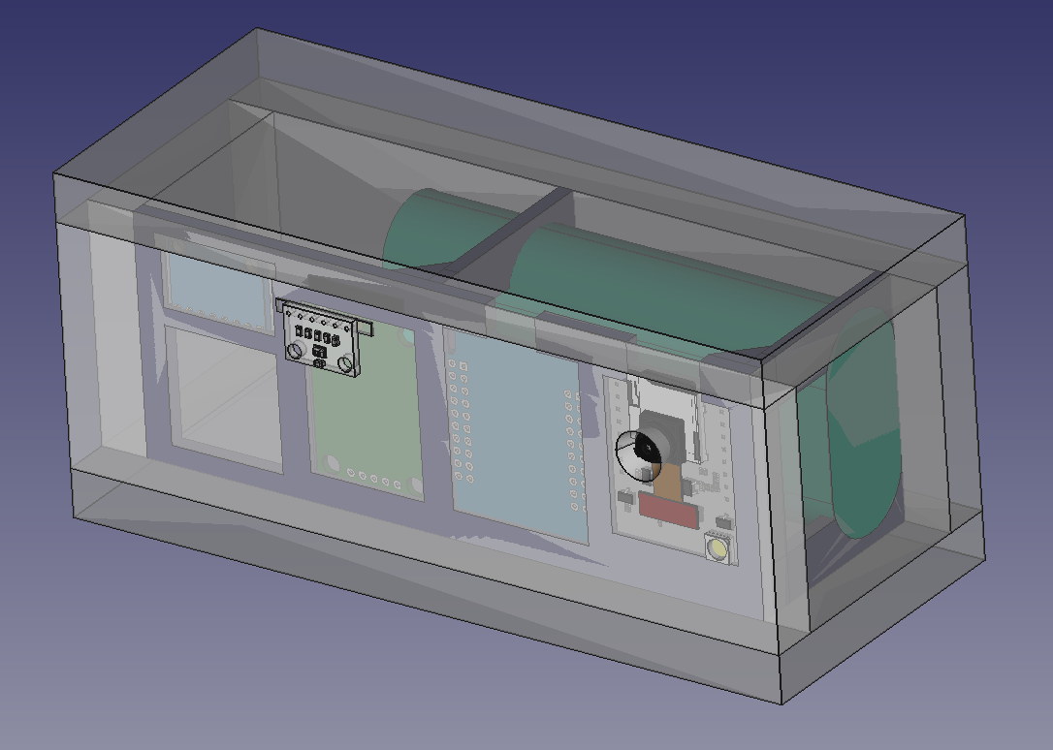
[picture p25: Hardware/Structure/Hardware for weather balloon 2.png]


The FreeCAD design files are here: https://github.com/jmwislez/fli3d/tree/master/Hardware/Structure

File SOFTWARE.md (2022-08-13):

# Fli3d software

The software for Fli3d is developed in Arduino IDE.  It runs on two ESP32 boards (https://github.com/jmwislez/fli3d-esp32.git and https://github.com/jmwislez/fli3d-esp32cam.git), using a common library (https://github.com/jmwislez/fli3d-lib.git).

## Initialisation

The `setup()` part of the sketch initializes all services at power on:



A typical TM reporting of the initialisation is shown below:




## Loop

The `loop()` part of the sketch performs the measurements and maintanance tasks.  This is shown below for the ESP32 board:



## Telemetry transmission

Telemetry can be sent over different channels:
* CCSDS packets over WiFi/UDP to Yamcs ground station
* CCSDS packets to local file system (LittleFS flash on ESP32, and SD-card or LittleFS flash on ESP32cam) for post-flight recovery and in-flight buffering
* JSON packets on SD-card (on ESP32cam) for post-flight recovery 
* CCSDS or JSON packets over Serial to the other on-board ESP32 (or for in-development debug)
* JSON packets over WiFi/UDP to a debug interface
* a summary CCSDS packet over 433 MHz/OOK radio transmission

There is also a routing table, allowing to define for each individual packet type (APID) whether it is or is not routed on a particular channel.



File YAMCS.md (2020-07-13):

# Using Yamcs for Fli3d

## Introduction

Fli3d is a small ESP32-based payload developed for fun.  It is designed to be put on-board a microrocket, which is due to reach an altitude of about 100m.  The payload will perform measurements during the flight (images, gps, accelerometer/gyrometer, barometer), will store these on an SD, and also transmit the data to ground in real-time over WiFi and over 433 MHz radio.

More information about Fli3d can be found here: https://github.com/jmwislez/fli3d/.

For receiving, monitoring, displaying and storing the real-time data, I was looking for the appropriate software.  Yamcs seemed especially suited, since it is designed to do exactly this, only for real space systems.

This page discusses how I configured Yamcs for this purpose.

## Telemetry format

Originally, the telemetry generated by the ESP32 was based on JSON messages, transmitted directly over UDP, or via a MQTT server.  While this is very convenient to implement and use for logging and debugging, it is of course inefficient in its use of bandwidth, which may become an issue when the rocket is getting high and the WiFi connection bad.  Also, Yamcs at this stage does not work with JSON or MQTT out of the box, so I quickly decided to take the benefit of the constraint and to transmit the telemetry as compact CCSDS packages to a TCP port, the latter to ensure error correction when the connection worsens. 

## Sending telemetry packets from ESP32

Demo Arduino code for generating CCSDS packets and sending these to Yamcs over UDP is provided here: https://github.com/jmwislez/fli3d/tree/master/Yamcs/esp32-demo.  The functional code used in Fli3d is in https://github.com/jmwislez/fli3d_lib

The CCSDS format is described in https://public.ccsds.org/Pubs/133x0b1c2.pdf. 

## Setting up Yamcs

I installed Yamcs on a Ubuntu 16.04 computer, following the instructions on https://yamcs.org/getting-started.  After ensuring it works with the provided example, I started tuning this example to my system.  

This is what I needed to adapt to start:
 - Updated ```src/main/yamcs/etc/yamcs.yaml```  
 - Created ```src/main/yamcs/etc/yamcs.fli3d.yaml``` based on ```yamcs.myproject.yaml```
 - Created ```src/main/yamcs/mdb/xtce.fli3d.mdb``` based on ```xtce.mdb```, and reworked it to define my telemetry test packet (pretty straightforward for basic stuff).
All three these files are found in https://github.com/jmwislez/fli3d/tree/master/Yamcs/yamcs-server.  Note that corresponding configuration files for esp32-demo are available there too.

Re-starting Yamcs, I got parsing and compiling errors and warnings for the ```xtce.fli3d.mdb``` file until I got it right.  Nice!  After that, as a charm my telemetry was visible in the Yamcs web application!

In order to set up the latest Yamcs server instead of the demo version, install the precompiled package from https://github.com/yamcs/yamcs/releases.  Copy your configuration files to ```etc/``` and ```mdb/```, and you're done.

With this initial end-to-end test in place, I could further extend this, to implement all the functionality I need:
 - setting up and configuring Yamcs Studio for synoptic displays
 - adding multiple packets and improving the MDB
 - setting up the packet viewer 
 - adding event packets
 - moving to TCP
 - introducing telecommands
 - introducing archiving

## Setting up Yamcs Studio

I first tried by downloading Yamcs Studio from github (https://github.com/yamcs/yamcs-studio), unzipping it, and compiling it using the “make” command, just as explained on github.  From there, I consulted the documentation in https://yamcs.org/media/yamcs-studio.pdf, but could not get any further.  The next step was impossible to guess: starting Yamcs Studio goes by the following command:
```releng/org.yamcs.studio.editor.product/target/products/yamcs-studio/linux/gtk/x86_64/yamcs-studio-1.3.4-SNAPSHOT/Yamcs\ Studio```

While getting this answer from the developers, I got the advise to rather get a precompiled version from https://github.com/yamcs/yamcs-studio/releases .  That was much easier, indeed.

Some interesting windows like “Archive” and “Data Links” are not activated by default, so this needs to be done first through "Windows" / "Show View" / "Others...". 

The learning curve for creating synoptic displays with the Display Builder is not steep.  The interface has some glitches and pecularities, but these are easily worked around once known.  It is also very easy to have both Display Builder and Display Runner open, as this allows to test changes in displays immediately.

The displays I created for Fli3d and for esp32-demo are here: https://github.com/jmwislez/fli3d/tree/master/Yamcs/yamcs-studio

## Adding multiple packets and improving the Mission Database

This was easy: I just had to have my payload send different packets over different APIDs, and define these packets in ```xtce.fli3d.xml```.

Further editing of the ```src/main/yamcs/mdb/xtce.fli3d.xml``` MDB definition file can be done following the format description in https://public.ccsds.org/Pubs/660x1g1.pdf. Be sure to edit the file in src, and not the file in target as I accidentally did a few times.  It happened to me by accident and I lost my updates.  Additions are:
  - add measurement units
  - add enumeration labels
  - define correct endianness of multi-byte data.  In the XTCE file, uint16_t should be defined as ```<IntegerDataEncoding encoding="unsigned" sizeInBits="16" byteOrder="leastSignificantByteFirst" />``` to correctly interpret data encoded by ESP32.

Note that if you define a series of sub-byte elements in the packed struct on the ESP32, these are interpreted in reversed sequence on Yamcs.  

## Setting up the Packet Viewer

There is a rudimentary packet viewer in the Yamcs Server web interface, but the Packet Viewer application is more powerful and user friendly.  And it does decode the telemetry packets. The best way to get the Packet Viewer is from the Yamcs release page: https://github.com/yamcs/yamcs/releases.

Use the item under the File menu to connect to your running Yamcs server, not forgetting to set the instance (in our case "fli3d" or "esp32-demo"), and tick "Server MDB".  You should see packets come in in real time, and be able to click on them for analysis. Nice!

## Adding Event packets

## Moving to TCP

## Introducing telecommanding

## Introducing archiving

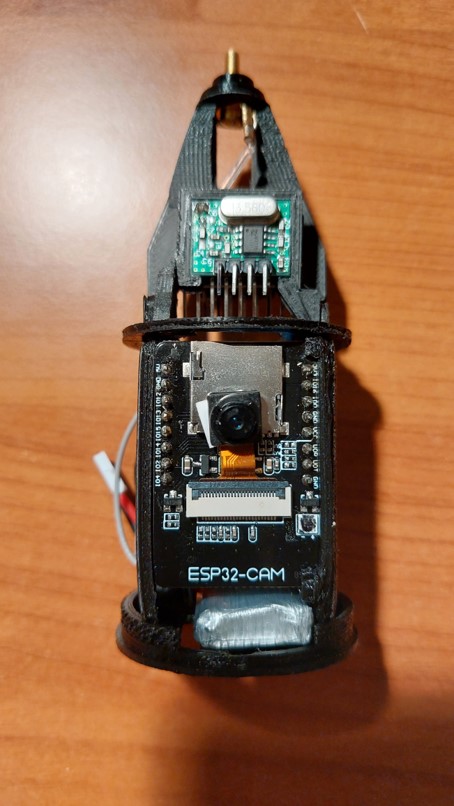
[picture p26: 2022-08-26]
Pictures/Fli3d for micro-rocket/Hardware for Fli3d Aubergine.jpg

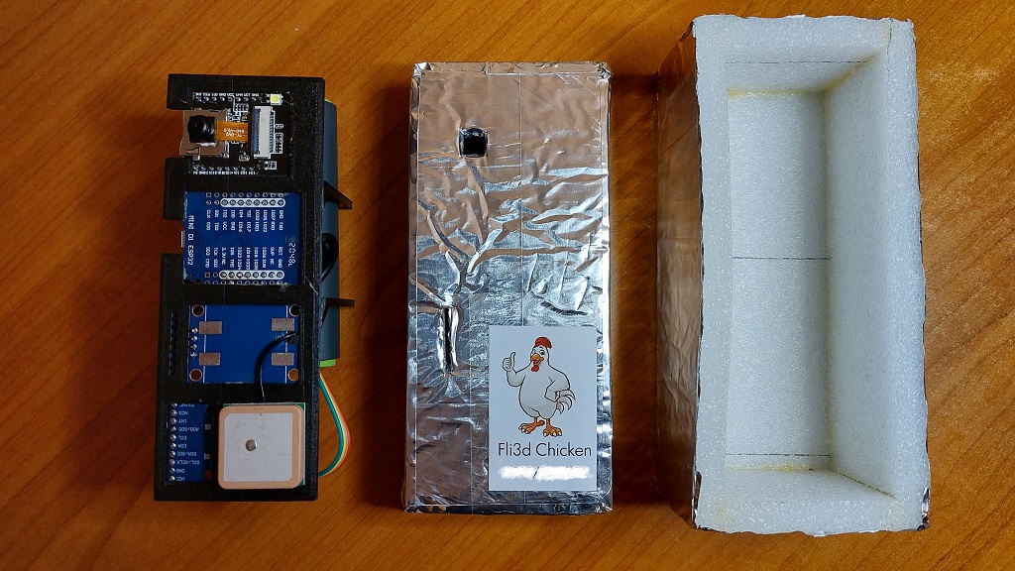
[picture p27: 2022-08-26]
Pictures/Fli3d for weather balloon/Hardware for Fli3d Chicken.jpg

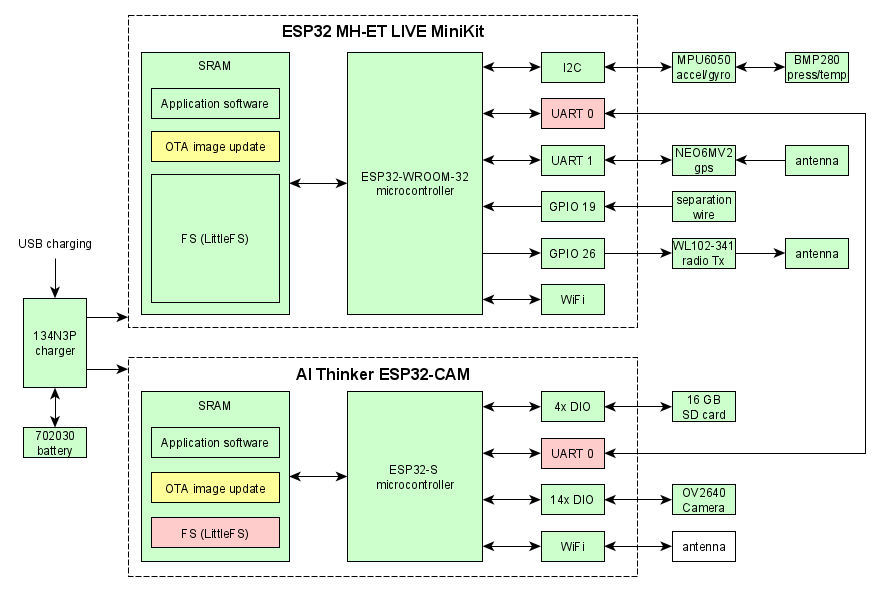
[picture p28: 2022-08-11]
Hardware/Electronics/Fli3d electronics.png

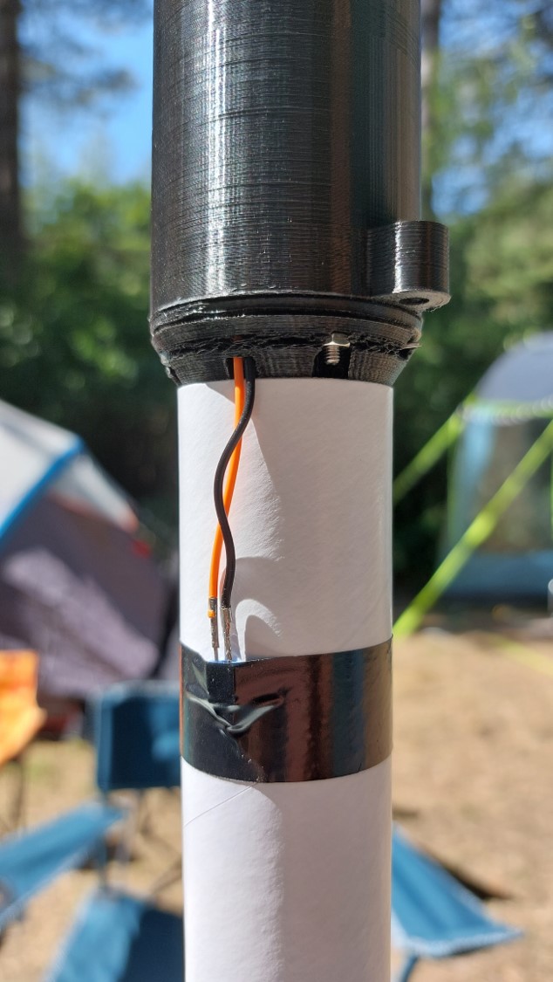
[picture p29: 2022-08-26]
Pictures/Fli3d for micro-rocket/Separation detection.jpg

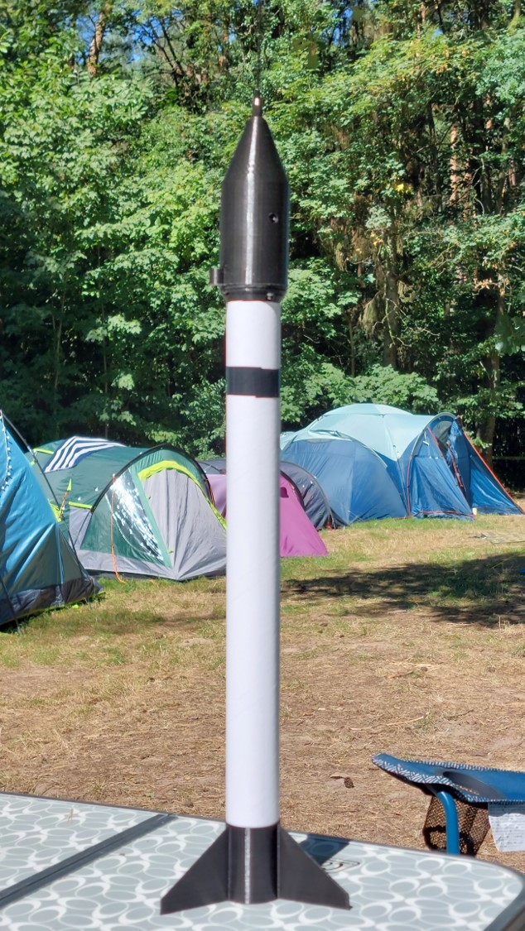
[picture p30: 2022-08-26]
Pictures/Fli3d for micro-rocket/Full rocket.jpg

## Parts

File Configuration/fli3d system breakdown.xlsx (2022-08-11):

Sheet: CIDL
 |  |  |  |  | budget |  |  | actual
ID | Item | Part identification | Type | Qty | mass (g) | I typ (mA) | I peak (mA) | mass (g) | I typ (mA) | Cost | Comments
1.0.0 | Assembly - top |  |  |  | 18.02 |  |  | 16.03 |  | €5.88
1.1.0 | Structure - top |  |  |  | 6.00 |  |  | 5.11 |  | €0.13
1.1.1 | Top baseplate |  | 3D print | 1 |  |  |  | 1.47 |  | €0.04 | printed in PLA
1.1.2 | MPU6050 support |  | 3D print | 1 |  |  |  | 1.97 |  | €0.05 | printed in PLA
1.1.3 | BMP280 support |  | 3D print | 1 |  |  |  | 0.43 |  | €0.01 | printed in PLA
1.1.4 | WL102 support |  | 3D print | 1 |  |  |  | 0.73 |  | €0.02 | printed in PLA
1.1.5 | Antenna support |  | 3D print | 1 |  |  |  | 0.51 |  | €0.01 | printed in PLA
1.2.0 | Electronics - top |  |  |  | 9.02 |  |  | 7.11 |  | €5.59
1.2.1 | 433 MHz antenna |  | EEE assy | 1 | 3.00 |  |  | 3.12 |  | €4.14
1.2.2 | 433 MHz transmitter | WL102-341 | EEE assy | 1 | 2.00 | ? |  | 1.41 |  | €0.47 | mass with header
1.2.3 | Accelerometer/gyroscope | MPU6050 | EEE assy | 1 | 2.72 | 3.90 |  | 1.67 |  | €0.57 | mass with header
1.2.4 | Barometer | BMP280 | EEE assy | 1 | 1.30 | 0.0027 |  | 0.91 |  | €0.41 | mass with header
1.3.0 | Fasteners - top |  |  |  | 3.00 |  |  | 3.52 |  | €0.16
1.3.1 |  | M3x14 | fasteners | 1 | 1.00 |  |  | 0.77 |  | €0.02
1.3.2 |  | M3 nut | fasteners | 1 |  |  |  | 0.31 |  | €0.02
1.3.3 |  | M2.5x6 | fasteners | 4 | 2.00 |  |  | 1.56 |  | €0.06
1.3.4 |  | M2.5 nut | fasteners | 4 |  |  |  | 0.88 |  | €0.06
1.4.0 | Harness - top |  |  |  |  |  |  | 0.29
1.4.1 | Antenna harness |  | harness | 1 |  |  |  | 0.29
2.0.0 | Assembly - centre |  |  |  | 54.10 |  |  | 39.53 |  | €15.89
2.1.0 | Structure - centre |  |  |  | 14.00 |  |  | 8.49 |  | €0.21
2.1.1 | Baseplate |  | 3D print | 1 |  |  |  | 3.01 |  | €0.08 | printed in PLA
2.1.2 | Sideplate 1 |  | 3D print | 1 |  |  |  | 3.98 |  | €0.10 | printed in PLA
2.1.3 | Sideplate 2 |  | 3D print | 1 |  |  |  | 1.50 |  | €0.04 | printed in PLA
2.2.0 | Electronics - centre |  |  |  | 40.10 |  |  | 31.04 |  | €15.68
2.2.1 | Core processor | ESP32 minikit MH-ET Live | EEE assy | 1 | 3.00 | 100.00 | 200.00 | 7.99 |  | €1.92 | mass with header
2.2.2 | Camera module | ESP32-CAM | EEE assy | 1 | 10.00 | 180.00 |  | 7.81 |  | €5.10 | mass with header
2.2.3 | Camera | OV2640 | EEE assy | 1 |  |  |  | 0.40 |  | €0.00 | cost included in Camera module
2.2.4 | GPS receiver | NEO6MV2 | EEE assy | 1 | 17.60 | 67.00 |  | 2.98 |  | €3.22 | mass without header
2.2.5 | GPS antenna |  | EEE assy | 1 |  |  |  | 3.02 |  | €0.00 | cost included in GPS receiver
2.2.6 | WiFi antenna |  | EEE assy | 1 | 1.00 |  |  | 0.72 |  | €1.13 | NOT MOUNTED
2.2.7 | Battery | 702030 (300 mAh) | EEE assy | 1 | 8.20 |  |  | 7.85 |  | €1.70
2.2.8 | SD card |  | EEE assy | 1 | 0.30 |  |  | 0.27 |  | €2.61
2.3.0 | Fasteners - centre
2.3.1 |  | M2.5x6 | fasteners | 5 | 8.00 |  |  | 1.88 |  | €0.08
2.3.2 |  | M2.5 nut | fasteners | 5 |  |  |  | 1.11 |  | €0.08
2.3.3 |  | M3x12 | fasteners | 2 | 2.00 |  |  | 1.46 |  | €0.11
2.3.4 |  | M3 nut | fasteners | 2 |  |  |  | 0.62 |  | €0.03
2.4.0 | Harness - centre
2.4.1 | Radio transmitter harness |  | harness | 1 |  |  |  | 1.19
2.4.2 | MPU+BMP harness |  | harness | 1
2.4.3 | GPS harness |  | harness | 1
2.4.4 | Camera serial harness |  | harness | 1 |  |  |  | 0.58
2.4.5 | Camera power harness |  | harness | 1
2.4.6 | Power distribution (5V/GND) |  | harness | 1 |  |  |  | 2.35
3.0.0 | Assembly - bottom |  |  |  | 11.00 |  |  | 10.73 |  | €0.67
3.1.0 | Structure - bottom |  |  |  | 5.00 |  |  | 7.01 |  | €0.18
3.1.1 | Structure - bottom |  | 3D print | 1 | 5.00 |  |  | 7.01 |  | €0.18 | printed in PLA
3.2.0 | Electronics - bottom |  |  |  | 2.00 |  |  | 1.40 |  | €0.32
3.2.1 | Battery charger | 134N3P | EEE assy | 1 | 2.00 |  |  | 1.40 |  | €0.32 | with USB connector unsoldered
3.3.0 | Fasteners - bottom |  |  |  | 4.00 |  |  | 2.32 |  | €0.18
3.3.1 |  | M2.5x6 | fasteners | 3 | 3.00 |  |  | 1.12 |  | €0.05
3.3.2 |  | M2.5 nut | fasteners | 3 |  |  |  | 0.67 |  | €0.05
3.3.3 |  | Eye screw | fasteners | 1 | 1.00 |  |  | 0.53 |  | €0.08
3.4.0 | Harness - bottom
3.4.1 | Power harness |  | harness | 1
3.4.2 | Separation harness |  | harness | 1
4.0.0 | Assembly - external |  |  |  | 11.00 |  |  | 9.70 |  | €0.24
4.1.0 | Structure - external |  |  |  | 11.00 |  |  | 9.70 |  | €0.24
4.1.1 | Structure - external |  | 3D print | 1 | 11.00 |  |  | 9.70 |  | €0.24 | printed in PLA
 |  |  |  |  | 94.12 | 350.90 | 200.00 | 75.99 | 0.00 | €22.69

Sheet: wiring
ESP32 mini

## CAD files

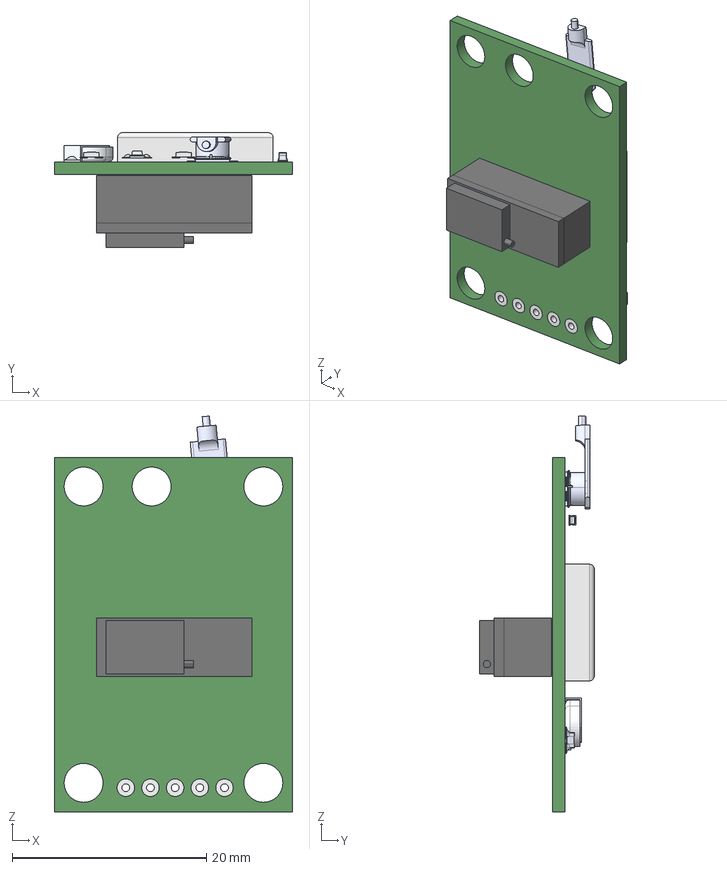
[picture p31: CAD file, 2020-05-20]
Hardware/Electronics/NEO6MV2 gps/neo6mv2.FCStd
24.5 x 11.8 x 40.8 mm
GPS_cap
GPS_res221
GPS_res472
GPS_res473
GPS_battery
GPS_res474
GPS_res100
GPS_led
GPS_connector
Antenna_connector
Antenna
contact
PCB
neo6m chip
contact001
contact002
contact003
contact004

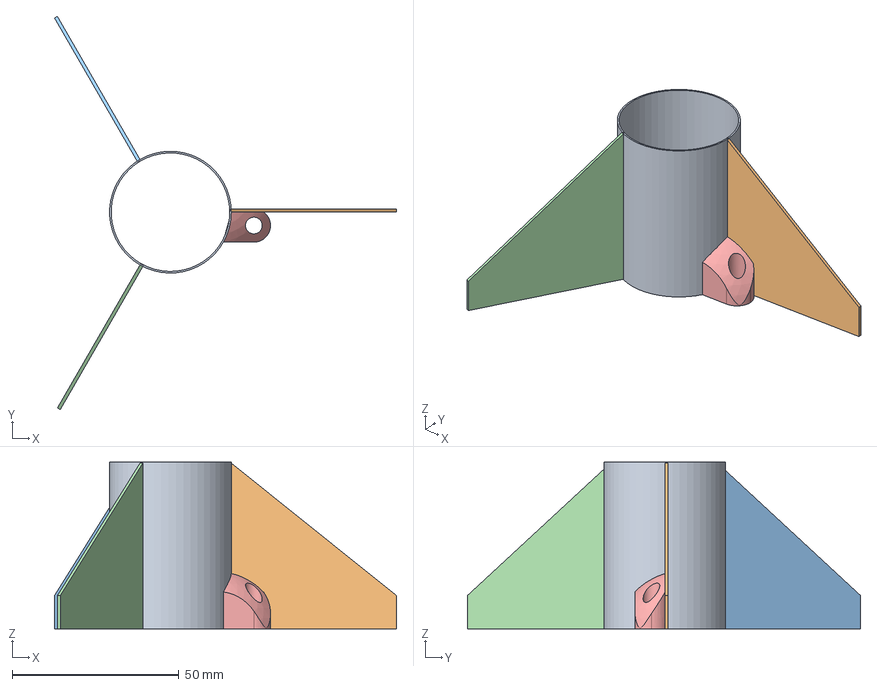
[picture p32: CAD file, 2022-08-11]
Hardware/Structure/fli3d fins v1.1.FCStd
102.5 x 117.8 x 50.0 mm
Tube
Fin 001
Fin 002
Fin 003
Slider

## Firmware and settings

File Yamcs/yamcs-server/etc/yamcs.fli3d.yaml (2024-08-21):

services:
  - class: org.yamcs.archive.XtceTmRecorder
  - class: org.yamcs.archive.ParameterRecorder
  - class: org.yamcs.archive.AlarmRecorder
  - class: org.yamcs.archive.EventRecorder
  - class: org.yamcs.archive.ReplayServer
  - class: org.yamcs.archive.CcsdsTmIndex
  - class: org.yamcs.parameter.SystemParametersCollector
    args:
      provideJvmVariables: true
      provideFsVariables: true
  - class: org.yamcs.ProcessorCreatorService
    args:
      name: realtime
      type: realtime
  - class: org.yamcs.archive.CommandHistoryRecorder
  - class: org.yamcs.parameterarchive.ParameterArchive
    args:
      realtimeFiller:
        enabled: false
      backFiller:
        enabled: true
        warmupTime: 60

dataLinks:
  - name: esp32-udp-in
    class: org.yamcs.tctm.UdpTmDataLink
    stream: tm_realtime
    port: 10042
    packetPreprocessorClassName: org.yamcs.tctm.GenericPacketPreprocessor
    packetPreprocessorArgs:
      timestampOffset: -1
      seqCountOffset: -1
  - name: esp32-udp-out-fli3d
    class: org.yamcs.tctm.UdpTcDataLink
    stream: tc_realtime
    host: 192.168.5.177
    port: 10052
  - name: esp32-udp-out-AndroidAP2CDC
    class: org.yamcs.tctm.UdpTcDataLink
    stream: tc_realtime
    host: 192.168.133.98
    port: 10052
  - name: esp32-udp-out-wrt54
    class: org.yamcs.tctm.UdpTcDataLink
    stream: tc_realtime
    host: 192.168.10.3
    port: 10052
  - name: esp32-udp-out-wlan-27
    class: org.yamcs.tctm.UdpTcDataLink
    stream: tc_realtime
    host: 192.168.2.184
    port: 10052   
  - name: esp32-udp-out-fri3d-legacy
    class: org.yamcs.tctm.UdpTcDataLink
    stream: tc_realtime
    host: 192.168.2.184
    port: 10052       
  - name: esp32cam-udp-in
    class: org.yamcs.tctm.UdpTmDataLink
    stream: tm_realtime
    port: 10043
    packetPreprocessorClassName: org.yamcs.tctm.GenericPacketPreprocessor
    packetPreprocessorArgs:
      timestampOffset: -1
      seqCountOffset: -1    
  - name: esp32cam-udp-out-fli3d
    class: org.yamcs.tctm.UdpTcDataLink
    stream: tc_realtime
    host: 192.168.5.177
    port: 10053
  - name: esp32cam-udp-out-AndroidAP2CDC
    class: org.yamcs.tctm.UdpTcDataLink
    stream: tc_realtime
    host: 192.168.133.98
    port: 10053
  - name: esp32cam-udp-out-wrt54
    class: org.yamcs.tctm.UdpTcDataLink
    stream: tc_realtime
    host: 192.168.10.3
    port: 10053
  - name: esp32cam-udp-out-wlan-27
    class: org.yamcs.tctm.UdpTcDataLink
    stream: tc_realtime
    host: 192.168.2.199
    port: 10053   
  - name: esp32cam-udp-out-fri3d-legacy
    class: org.yamcs.tctm.UdpTcDataLink
    stream: tc_realtime
    host: 192.168.2.184
    port: 10053          
  - name: radio-udp-in
    class: org.yamcs.tctm.UdpTmDataLink
    stream: tm_realtime
    port: 10044
    packetPreprocessorClassName: org.yamcs.tctm.GenericPacketPreprocessor
    packetPreprocessorArgs:
      timestampOffset: -1
      seqCountOffset: -1
  - name: tm_file
    class: org.yamcs.tctm.FilePollingTmDataLink
    stream: tm_dump
    incomingDir: C:\Users\jmw\Documents\yamcs-5.7.5\files_for_tm_dump
    packetInputStreamClassName: org.yamcs.tctm.CcsdsPacketInputStream
    packetPreprocessorClassName: org.yamcs.tctm.GenericPacketPreprocessor
    packetPreprocessorArgs:
      timestampOffset: -1
      seqCountOffset: -1
mdb:
  # Configuration of the active loaders
  # Valid loaders are: sheet, xtce or fully qualified name of the class
  - type: xtce
    args:
      file: C:\Users\jmw\Documents\fli3d\Yamcs\yamcs-server\mdb\xtce.fli3d.xml

# Configuration for streams created at server startup
streamConfig:
  tm:
    - name: "tm_realtime"
    - name: "tm_dump"
  cmdHist: ["cmdhist_realtime", "cmdhist_dump"]
  event: ["events_realtime", "events_dump"]
  param: ["pp_realtime", "sys_param", "proc_param"]
  parameterAlarm: ["alarms_realtime"]
  tc: ["tc_realtime"]

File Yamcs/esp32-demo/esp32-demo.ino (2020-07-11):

#define PKT_TM        0 
#define PKT_TC        1
#define APID_OFFSET   100
#define NUMBER_OF_PID 2

#include <WiFi.h>
#include "WiFiUdp.h"

WiFiUDP wifiUDP;

char*    wifi_ssid = "your_wifi_ssid";
char*    wifi_password = "your_wifi_password";
char*    yamcs_server = "your_ip_address";
uint16_t yamcs_tm_port = 10015;

struct __attribute__ ((packed)) ccsds_hdr_t {
  uint8_t  apid_H:3;                // 0:5
  bool     sec_hdr:1;               // 0: 4
  bool     type:1;                  // 0:  3
  uint8_t  version:3;               // 0:   0
  uint8_t  apid_L;                  // 1
  uint8_t  seq_ctr_H:6;             // 2:2
  uint8_t  seq_flag:2;              // 2: 0
  uint8_t  seq_ctr_L;               // 3
  uint8_t  pkt_len_H;               // 4
  uint8_t  pkt_len_L;               // 5
} ccsds_hdr;

struct __attribute__ ((packed)) packet1_t {
  uint32_t millis:24;               // 0+1+2
  uint16_t ctr;                     // 3+4
  uint8_t  mode:4;                  // 5:4
  bool     bool1:1;                 // 5: 3
  bool     bool2:1;                 // 5:  2
  bool     bool3:1;                 // 5:   1
  bool     bool4:1;                 // 5:    0
  float    pressure;                // 6+7+8+9
} packet1;

struct __attribute__ ((packed)) packet2_t {
  uint32_t millis:24;               // 0+1+2
  uint16_t ctr;                     // 3+4
  float    value1;                  // 5+6+7+8
  float    value2;                  // 9+10+11+12
} packet2;

void ccsds_publish (uint16_t PID, char* payload_ptr, uint16_t payload_len) {
  update_ccsds_hdr (PID, PKT_TM, payload_len);
  wifiUDP.beginPacket(yamcs_server, yamcs_tm_port);
  wifiUDP.write ((const uint8_t*)&ccsds_hdr, sizeof (ccsds_hdr_t));
  wifiUDP.write ((const uint8_t*)payload_ptr, payload_len); 
  wifiUDP.endPacket();
}

void update_ccsds_hdr (uint16_t PID, bool pkt_type, uint16_t pkt_len) {
  static uint16_t ccsds_ctr[NUMBER_OF_PID+1];
  ccsds_ctr[PID]++;
  ccsds_hdr.version = 0;
  ccsds_hdr.type = pkt_type;
  ccsds_hdr.sec_hdr = false;
  ccsds_hdr.apid_H = (uint8_t)((PID + APID_OFFSET) >> 8);
  ccsds_hdr.apid_L = (uint8_t)(PID + APID_OFFSET);
  ccsds_hdr.seq_flag = 3;
  ccsds_hdr.seq_ctr_H = (uint8_t)(ccsds_ctr[PID] >> 8);
  ccsds_hdr.seq_ctr_L = (uint8_t)ccsds_ctr[PID];
  ccsds_hdr.pkt_len_H = (uint8_t)((pkt_len - 1) >> 8);
  ccsds_hdr.pkt_len_L = (uint8_t)(pkt_len - 1);
  Serial.print ("[version:");
  Serial.print (ccsds_hdr.version);
  Serial.print ("|type:");
  Serial.print (ccsds_hdr.type);
  Serial.print ("|sec_hdr:");
  Serial.print (ccsds_hdr.sec_hdr);
  Serial.print ("|apid:");
  Serial.print (256*ccsds_hdr.apid_H+ccsds_hdr.apid_L);
  Serial.print ("|ctr:");
  Serial.print (ccsds_ctr[PID]);
  Serial.print ("|len:");
  Serial.print (pkt_len - 1);
  Serial.println ("]");
}

void setup() {
  Serial.begin (115200);
  Serial.println ();
  WiFi.begin (wifi_ssid, wifi_password);
  Serial.print ("Connecting");
  while (WiFi.status () != WL_CONNECTED)
  {
    delay (500);
    Serial.print (".");
  }
  Serial.println ();
  Serial.print ("Connected, IP address: ");
  Serial.println (WiFi.localIP());
}

void loop() {
  static uint32_t next_second;
  if (millis() > next_second) {
    next_second = millis() + 1000;
    packet1.millis = millis();
    packet1.ctr++;
    packet1.mode = random (0,4);
    packet1.bool1 = false;
    packet1.bool2 = random (0,2);
    packet1.bool3 = random (0,2);
    packet1.bool4 = true;
    packet1.pressure = (float)(random (1000000,1013000))/1000;
    ccsds_publish (1, (char*)&packet1, sizeof(packet1));
    delay (500);
    packet2.millis = millis();
    packet2.ctr++;
    packet2.value1 = (float)(random (-10000,10000))/1000;
    packet2.value2 = -123.456;
    ccsds_publish (2, (char*)&packet2, sizeof(packet2));
  }
}

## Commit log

2020-05-20 Added components data files
    [134N3P .step, ESP32minikit.FCStd, WL102-341 approx.fcstd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]
2020-05-21 Added ESP32cam description
2020-05-22 Added battery section
2020-05-22 Added wiring and structure section
2020-05-22 Add hardware design files
    [fli3d launch adapter.fcstd, fli3d system breakdown.xlsx]
2020-05-22 Deleted double displays
    [fli3d launch adapter.fcstd]
2020-07-11 Added Yamcs configuration files for esp32-demo
2020-07-11 Added arduino demo software to generate CCSDS packets for Yamcs
2020-10-31 Completed update of motion, pressure and radio TM
2022-07-22 Update displays for redefined TM_ESP32CAM and TIMER_ESP32CAM packages
2022-07-25 Fine-tuned camera and radio packets
    [134N3P .step, ESP32minikit.FCStd, WL102-341 approx.fcstd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]
2022-08-05 Latest mechanical design, including fins
    [fli3d finns v1.0.FCStd, fli3d launch adapter.fcstd]
2022-08-11 Adding schematics describing software
2022-08-11 Cleanup and configuration update
    [fli3d finns v1.0.FCStd, fli3d fins v1.1.FCStd, fli3d system breakdown.xlsx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]
2022-08-13 moved files
    [fli3d fins v1.1.FCStd, neo6mv2.FCStd]
2022-08-13 Re-added accidentally deleted Structure files
    [fli3d fins v1.1.FCStd]
2022-09-10 Add TC/TM for opsmode freeze, temperature and magnetometer
2022-10-01 Added Fli3d Chicken flight report
    [Fli3d Chicken procedure.xlsx, Fli3d Chicken telemetry extraction.xlsx]
